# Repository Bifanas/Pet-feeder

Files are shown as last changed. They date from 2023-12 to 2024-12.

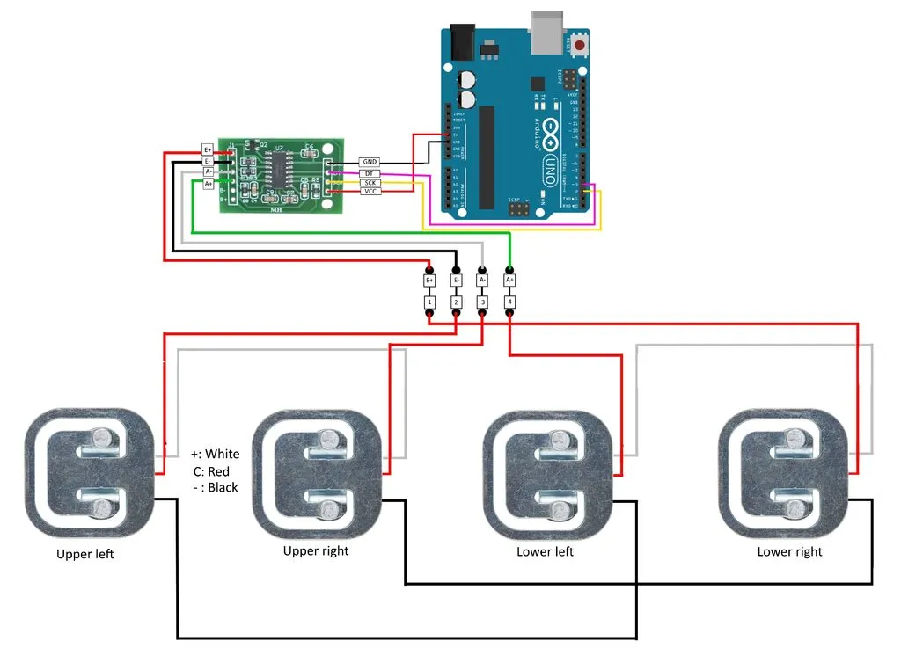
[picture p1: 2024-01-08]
Components testing/4-load-cells.png

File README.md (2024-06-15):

# Pet feeder 🐕

We designed an affordable dog feeder suitable for every kibble size and we hope that by sharing it, we can help more dog owners out there to create their perfect solution.



We are a small group of friends, designers, engineers, and dog owners. We needed to ensure our fluffy friends were always fed on time, even when we got stuck at school or work. And as we have large dogs any commercial solutions were unsuitable for our needs. That's how we started developing this dog feeder, first as a student project, and now as a passion. 

Our automated feeder is meant to help keep a consistent feeding schedule and ensure portion control. The design consists of 3d printed parts, a dispensing mechanism controlled by a motor, and a load cell to control the portion size. To run the dog feeder, it is important to set up a feeding schedule and also to manually calibrate the amount of food, that is being dispensed.

## Table of Contents
- [Features](#features)
- [List of Materials](#list)
- [Tutorials](#tutorials)
- [Contributing](#contributing)
- [Acknowledgments](#acknowledgments)

<br>

## Features
With this version of the automated feeder, you know exactly how many grams of food your dog was fed. 
Features include:
- manual calibration
- implemented load cell
- real time clock
- feeding schedule
- portion control and history log

<br>

## Contributing
1. Fork the repository
2. Create a new branch: `git checkout -b feature-name`
3. Make your changes and commit: `git commit -m "Add feature"`
4. Push to the branch: `git push origin feature-name`
5. Submit a pull request

<br>
## Acknowledgments
- Thanks to [Author Name](https://github.com/author) for the inspiration



The first version is available to solve the task of feeding your pet remotely.



Unique mechanism that is compatible with any size of dog kibble. 



It is possible to expand the storage size, for larger breads.

Assembly_2024-Jun-15_04-08-04PM-000_CustomizedView39398573342_png

Friendly and easy to maintain.

Assembly_2024-Jun-15_04-07-05PM-000_CustomizedView9829416363_png

Keep the previous meals' data to make sure your pet was fed the correct amount.

For the smallest to the biggest.

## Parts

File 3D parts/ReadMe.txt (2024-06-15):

This models were desingned to be able to fit into the most bascic printers.
No support is needed for any part. Recomend printing in PETG with a lower layer hight (<= 0.16mm).

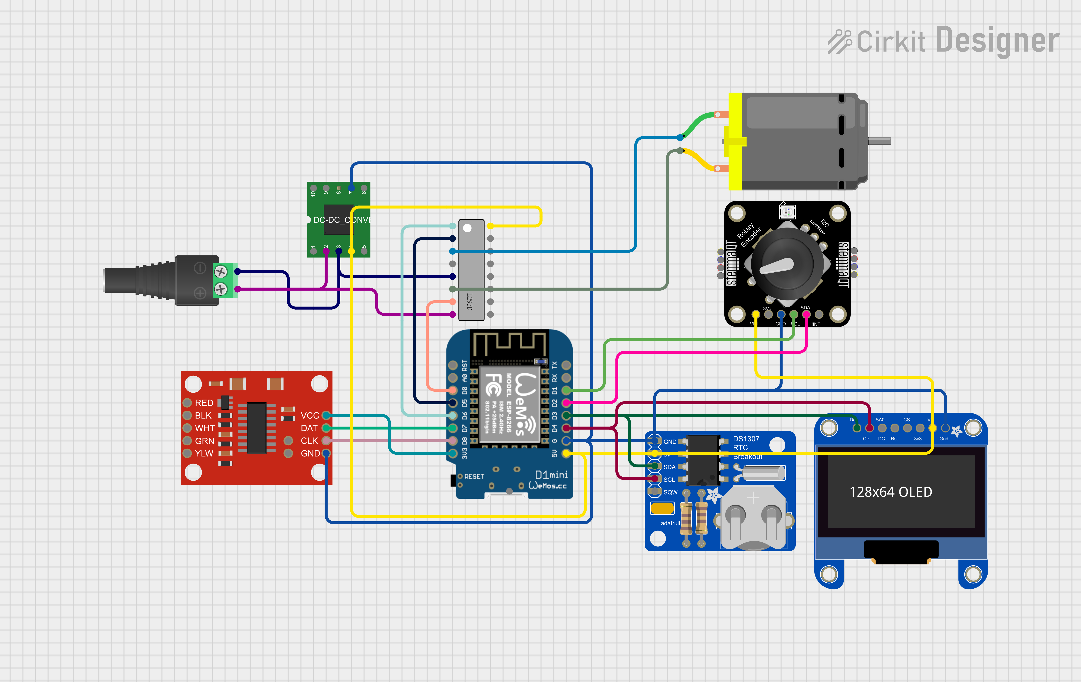
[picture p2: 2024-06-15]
Materials/circuit.png

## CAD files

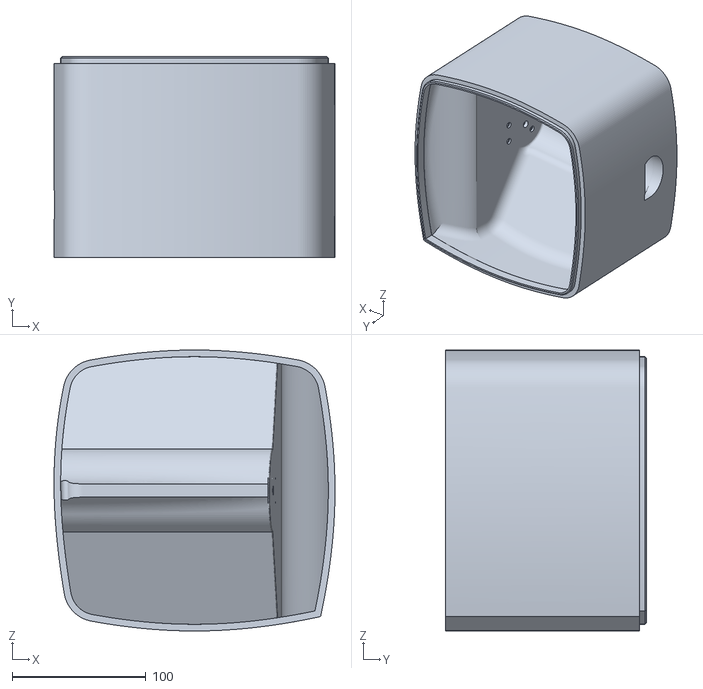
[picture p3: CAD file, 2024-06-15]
3D parts/Main.stl
210.0 x 150.0 x 210.0

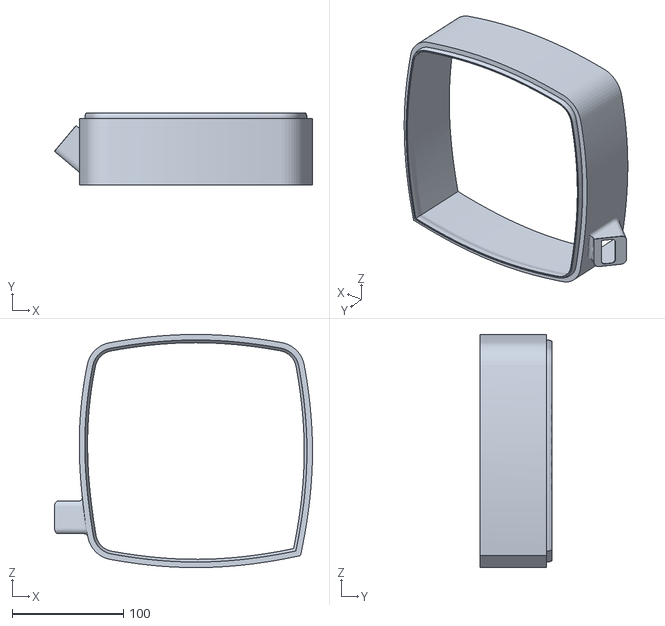
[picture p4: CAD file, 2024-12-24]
3D parts/Display adaptor.stl
232.3 x 65.0 x 210.0

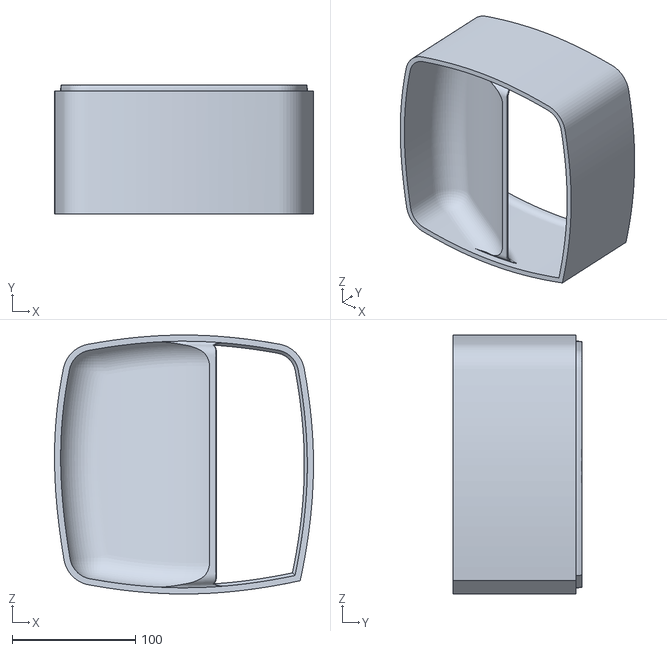
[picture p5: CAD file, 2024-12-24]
3D parts/Resivoir adaptor.stl
210.0 x 105.0 x 210.0

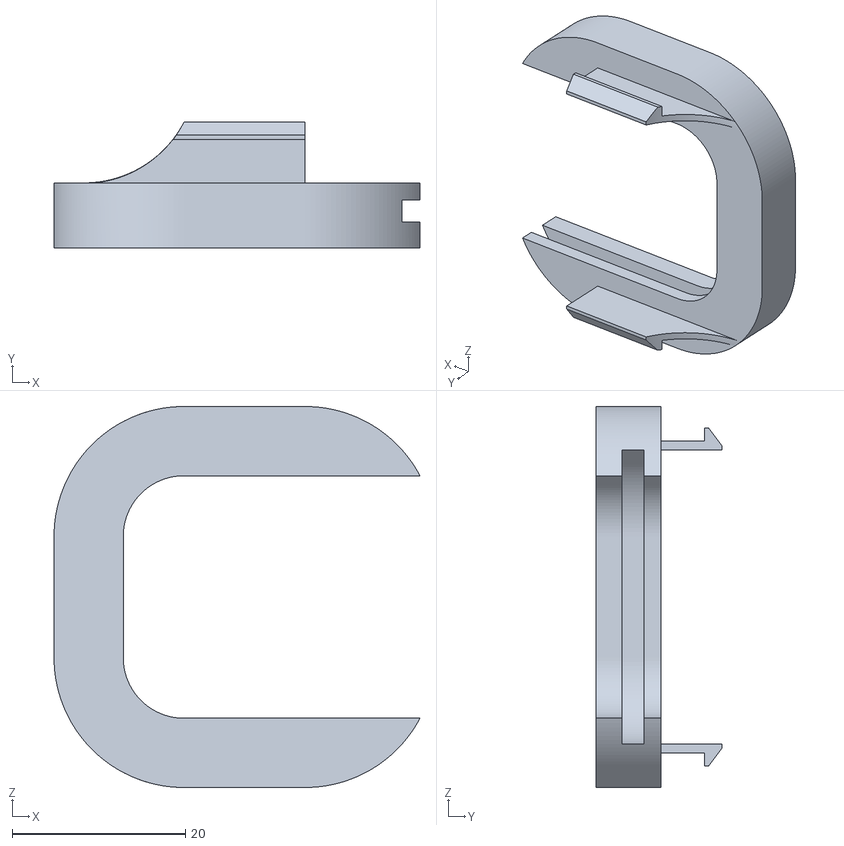
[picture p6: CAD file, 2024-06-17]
3D parts/Load cell.stl
42.3 x 14.5 x 44.0

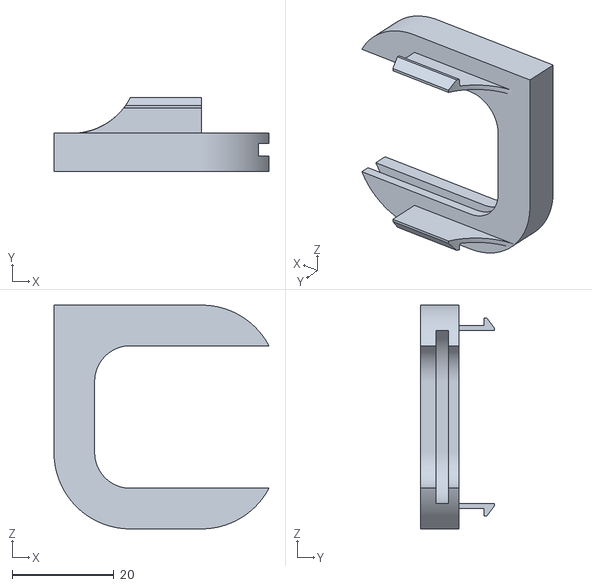
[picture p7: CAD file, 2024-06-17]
3D parts/Load cell corner.stl
42.3 x 14.5 x 44.0

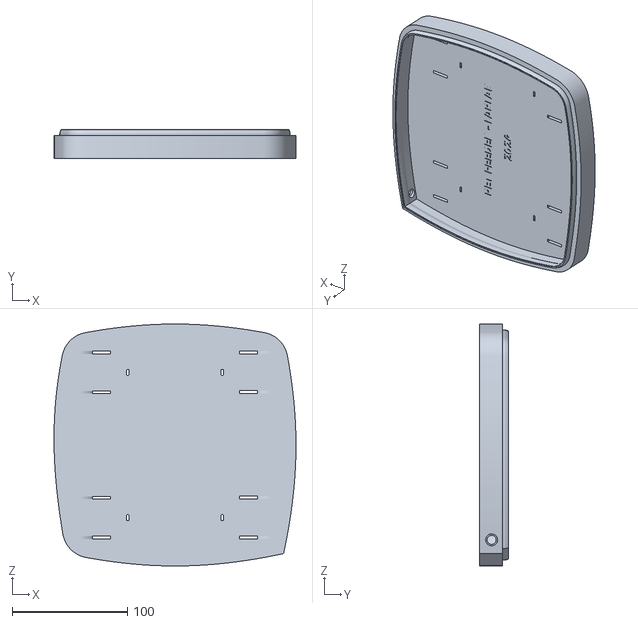
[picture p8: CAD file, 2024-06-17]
3D parts/Base.stl
210.0 x 25.0 x 210.0

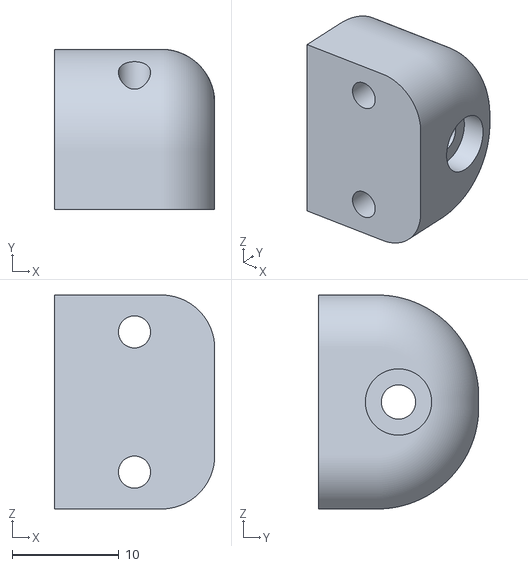
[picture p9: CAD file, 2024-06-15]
3D parts/motor atachment.stl
15.0 x 15.0 x 20.0

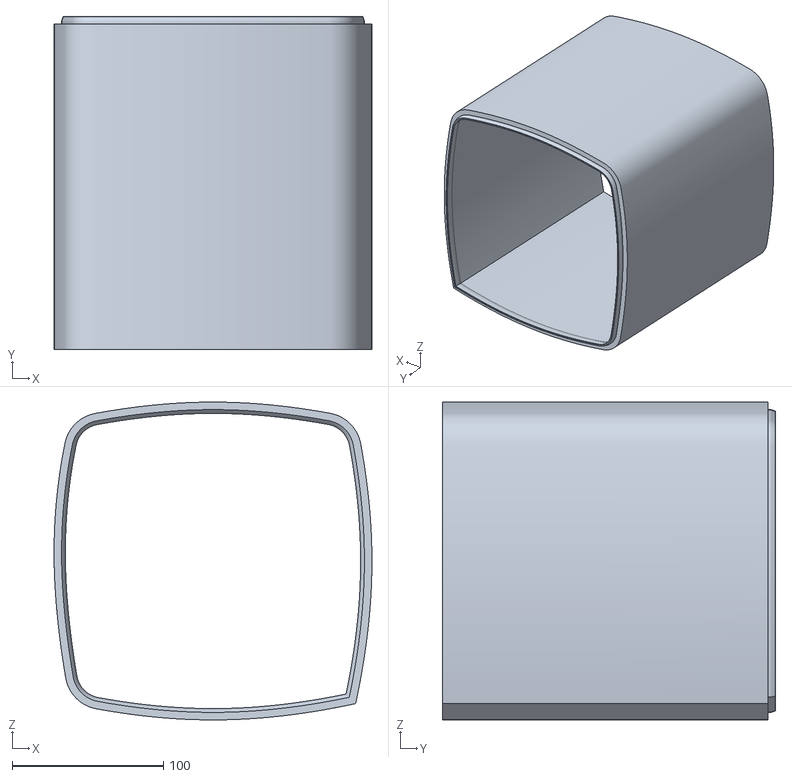
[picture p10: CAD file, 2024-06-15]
3D parts/Extension.stl
210.0 x 220.0 x 210.0

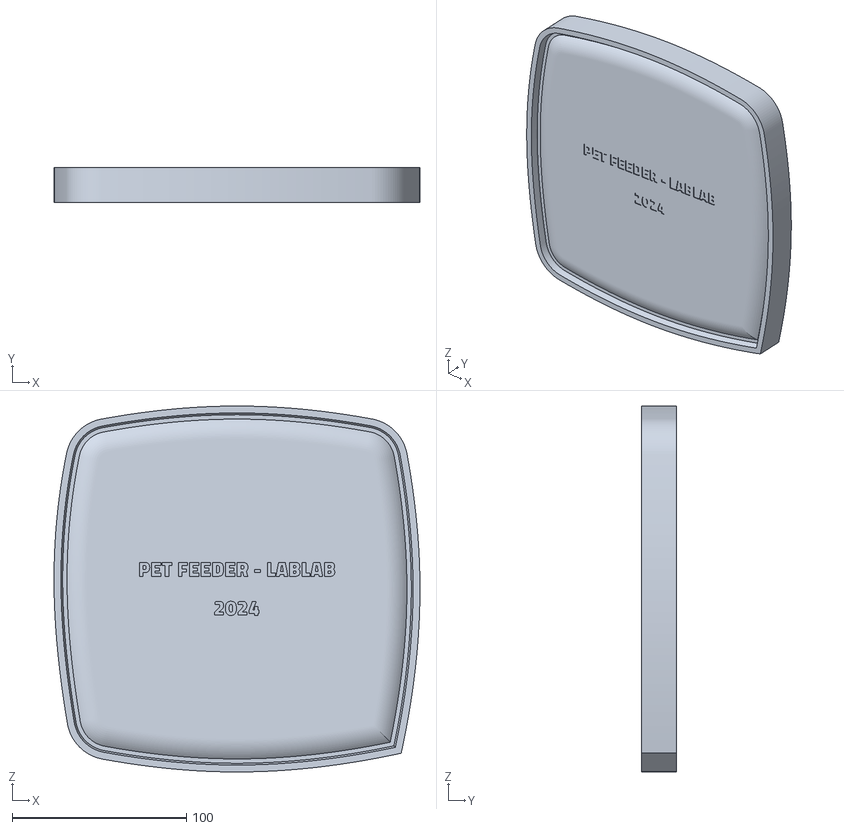
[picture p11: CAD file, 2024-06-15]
3D parts/Lid.stl
210.0 x 20.0 x 210.0

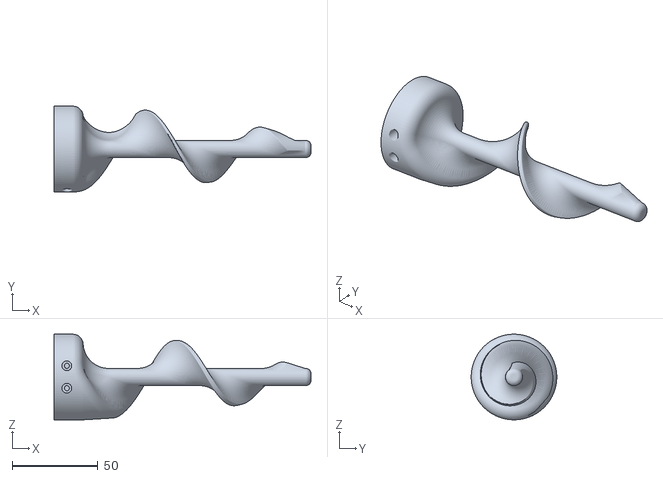
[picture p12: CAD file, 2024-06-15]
3D parts/Screw.stl
150.0 x 50.0 x 50.0

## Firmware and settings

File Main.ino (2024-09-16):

//////////////////////////////////////////////////////////////////
//                          LIBRARIES                           //
//////////////////////////////////////////////////////////////////

//LOAD CELL LIB-------------------------------------------------------------------------------------
#include "HX711.h"
HX711 scale;

//OLED DISP LIB-------------------------------------------------------------------------------------

#include <SPI.h>
#include <Wire.h>
#include <Adafruit_GFX.h>
#include <Adafruit_SSD1306.h>

// Real Time Clock LIB---------------------------------------------------------------------

#include "Arduino.h"
#include "uRTCLib.h"
uRTCLib rtc(0x68);  // uRTCLib rtc;

//////////////////////////////////////////////////////////////////
//                           DEFINES                            //
//////////////////////////////////////////////////////////////////

// LOAD CELL DEFINES--------------------------------------------------------------------------------

#define LOADCELL_DOUT_PIN 13
#define LOADCELL_SCK_PIN 15
float calibration_factor = 23.5; //need to czech

int weigth = 0;

// OLED DISP DEFINES--------------------------------------------------------------------------------

#define SCREEN_WIDTH 128  // OLED display width, in pixels
#define SCREEN_HEIGHT 64  // OLED display height, in pixels

// Declaration for SSD1306 display connected using I2C
#define OLED_RESET -1  // Reset pin
#define SCREEN_ADDRESS 0x3C
Adafruit_SSD1306 display(SCREEN_WIDTH, SCREEN_HEIGHT, &Wire, OLED_RESET);


const int bufferSize = 4;  // Size of the circular buffer
struct Measurement {
  char Calendar[20];
  float weight;
};

Measurement measurements[bufferSize];  // Array to store the measurements
int currentIndex = 0;                  // Index to keep track of the current position in the buffer

// RTC DEFINES--------------------------------------------------------------------------------

//char Calendar[20];  // string UTF8 end zero

// Motor DEFINES -----------------------------------------------------------------------------


 // Motor A connections
#define enA 17
#define in1 16
#define in2 14

float cal = 17.7;  // auxiliary declaration of an initial Calibration value
// calibration for 12V 28rpm float cal = 17.7;

int16_t Hour_A;  // 32767.. +32767  optimize the data type
int16_t Hour_B;

int16_t Minute_A;
int16_t Minute_B;

int16_t Meal_size_A;
int16_t Meal_size_B;


//////////////////////////////////////////////////////////////////
//                          FUNCTIONS                           //
//////////////////////////////////////////////////////////////////

void MotorControl(float time, bool direrction) {
  analogWrite(enA, 255); // Set motors to maximum speed

  if (direrction) {
    digitalWrite(in1, HIGH);  // 1 Forward
    digitalWrite(in2, LOW);
  } else if (!direrction) {  // 0 Reverse
    digitalWrite(in1, LOW);
    digitalWrite(in2, HIGH);
  }
  delay(time); // Keep spinning (Food control) 
  
  digitalWrite(in1, LOW); // Turn off motors
  digitalWrite(in2, LOW);

  analogWrite(enA, 0); // Disable the motors
}

//--------------------------------------------------------------------------------------


void feed(float cal, int amount) {
   float turns = 2900 * (50/ cal); //  (2900) = 1 tunr, 50g = portion size, cal = 18g per turn
  for (int i = 0; i < amount; i = i + 50) { // feeds in 50g pulses
  MotorControl(turns, 1); // Spins forward
  MotorControl(1000, 0);  // Spins backwards
  }
}


char now[20];

void addMeasurement(float newWeight, char current_calendar[]) {
  // Create a new measurement
  Measurement newMeasurement;
  strcpy(newMeasurement.Calendar, current_calendar);  // Use strcpy to copy the content
  newMeasurement.weight = newWeight;

  // Add the new measurement to the buffer at the current index
  measurements[currentIndex] = newMeasurement;

  // Increment the current index and wrap around if necessary
  currentIndex = (currentIndex + 1) % bufferSize;
}

void Main_screan_print() {
  //Serial.println("Buffer:");
  // Print the contents of the buffer

  /*
  for (int i = 0; i < bufferSize; i++) {
    Serial.print("Timestamp: ");
    Serial.print(measurements[i].Calendar);
    Serial.print(" Weight: ");
    Serial.println(measurements[i].weight, 2);
  }
  Serial.println();
  */

  display.clearDisplay();
  display.setTextSize(2);
  display.setTextColor(WHITE);
  display.setCursor(0, 0);
  display.print(rtc.hour());
  display.print(":");
  display.print(rtc.minute());
  display.print(":");
  display.print(rtc.second());
  display.setTextSize(1);
  display.print(" ");
  display.print(rtc.day());
  display.print("/");
  display.print(rtc.month());

  display.setCursor(0, 25);
  display.setTextSize(1);


  for (int i = 0; i < bufferSize; i++) {
   //display.print("");
    
    display.print(measurements[i].Calendar);
    display.print(" ");
    display.print(measurements[i].weight);
    display.println(" g");    
  }

  display.display();
}


void setup() {

  Serial.begin(9600);
  // MOTOR SETUP-----------------------------------------------------------------------------

  // Set all the motor control pins to outputs
  pinMode(enA, OUTPUT);
  pinMode(in1, OUTPUT);
  pinMode(in2, OUTPUT);

  // Turn off motors - Initial state
  digitalWrite(in1, LOW);
  digitalWrite(in2, LOW);

  // RTC SETUP-------------------------------------------------------------------------

  URTCLIB_WIRE.begin();

  //rtc.set(0,50,21, 6, 31, 8, 2024);  //(second, minute, hour, dayOfWeek, dayOfMonth, month, year)

  //LOAD CELL SETUP-------------------------------------------------------------------------------------

  scale.begin(LOADCELL_DOUT_PIN, LOADCELL_SCK_PIN);
  scale.set_scale(calibration_factor);      //Adjust to this calibration factor
  scale.tare();                             //Reset the scale to 0
  long zero_factor = scale.read_average();  //Get a baseline reading
  Serial.print("Zero factor: ");            //This can be used to remove the need to tare the scale. Useful in permanent scale projects.
  Serial.println(zero_factor);


  //OLED DISP SETUP-------------------------------------------------------------------------------------
  // initialize the OLED object
  if (!display.begin(SSD1306_SWITCHCAPVCC, SCREEN_ADDRESS)) {
    Serial.println(F("SSD1306 allocation failed"));
    for (;;)
      ;  // Don't proceed, loop forever
  }
  // Clear the buffer.
  display.clearDisplay();


  //////////////////////////////////////////////////////////////////
  //                    MEAL SCHEDULE SETUP                       //
  //////////////////////////////////////////////////////////////////

  // Change the time and size of the first meal!

  Hour_A = 8;
  Minute_A = 0;
  Meal_size_A = 200;

  // Change the time and size of the first meal!

  Hour_B = 17;
  Minute_B = 0;
  Meal_size_B = 200;
}

//////////////////////////////////////////////////////////////////
//                             MAIN                             //
//////////////////////////////////////////////////////////////////

int old_weigth = 0;
int new_weigth = 0;

unsigned long seconds = 1000L;  
unsigned long minutes = seconds * 60;



void loop() {
    //Updates the data ---------------------------------------------------------------------------------------

  rtc.refresh();  // Check the current time.

  sprintf(now, "%02d/%02d %02d:%02d", rtc.day(), rtc.month(), rtc.hour(), rtc.minute());
  Serial.println(now);

  Main_screan_print();

 // Serial.println(scale.get_units(5));  // Mesures how much food is inside.

  //schedule detection -------------------------------------------------------------------------------------
  if (Hour_A == rtc.hour() && Minute_A == rtc.minute() && 0 == rtc.second()) {

    old_weigth = scale.get_units(5);

    feed(cal, Meal_size_A);
    delay(5*minutes);

    new_weigth = scale.get_units(5);
    old_weigth = old_weigth - new_weigth;

    addMeasurement(old_weigth, now);
  }
  if (Hour_B == rtc.hour() && Minute_B == rtc.minute() && 0 == rtc.second()) {
    
    old_weigth = scale.get_units(5);
    
    feed(cal, Meal_size_B);
    delay(5*minutes);

    new_weigth = scale.get_units(5);
    old_weigth = old_weigth - new_weigth;
    addMeasurement(old_weigth, now);
  }
  delay(500);
}

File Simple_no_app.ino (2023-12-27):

//////////////////////////////////////////////////////////////////
//                          LIBRARIES                           //
//////////////////////////////////////////////////////////////////


//LOAD CELL LIB-------------------------------------------------------------------------------------
#include "HX711.h"
HX711 scale;

//OLED DISP LIB-------------------------------------------------------------------------------------

#include <SPI.h>
#include <Wire.h>
#include <Adafruit_GFX.h>
#include <Adafruit_SSD1306.h>

// Real Time Clock LIB---------------------------------------------------------------------

#include "Arduino.h"
#include "uRTCLib.h"
uRTCLib rtc(0x68);  // uRTCLib rtc;


//////////////////////////////////////////////////////////////////
//                           DEFINES                            //
//////////////////////////////////////////////////////////////////

// LOAD CELL DEFINES--------------------------------------------------------------------------------


#define LOADCELL_DOUT_PIN 18
#define LOADCELL_SCK_PIN 19
#define calibration_factor 106

int weigth = 0;


// OLED DISP DEFINES--------------------------------------------------------------------------------

#define SCREEN_WIDTH 128  // OLED display width, in pixels
#define SCREEN_HEIGHT 64  // OLED display height, in pixels

// Declaration for SSD1306 display connected using I2C
#define OLED_RESET -1  // Reset pin
#define SCREEN_ADDRESS 0x3C
Adafruit_SSD1306 display(SCREEN_WIDTH, SCREEN_HEIGHT, &Wire, OLED_RESET);

// RTC DEFINES--------------------------------------------------------------------------------

char Calendar[20];  // string UTF8 end zero

// Motor DEFINES -----------------------------------------------------------------------------

const int enable_motor = 15;
const int step = 2;
const int dirPin = 4;

float cal = 49;  // auxiliary declaration

int16_t Hour_A;  // 32767.. +32767
int16_t Hour_B;  // 32767.. +32767

int16_t Minute_A;  // 32767.. +32767
int16_t Minute_B;  // 32767.. +32767


int16_t Meal_size_A;  // 32767.. +32767
int16_t Meal_size_B;  // 32767.. +32767



//////////////////////////////////////////////////////////////////
//                          FUNCTIONS                           //
//////////////////////////////////////////////////////////////////


void stepper(float Screw_turns, int motorpin, bool direction) {

  int speed = 600;  //NEEDS TO BE CALIBRATED !!!
  int full_turn = 4000;

  int steps = Screw_turns * full_turn;  // get how many steps

  digitalWrite(enable_motor, LOW);
  digitalWrite(dirPin, direction);

  for (int x = 0; x < steps; x++) {
    digitalWrite(motorpin, HIGH);
    delayMicroseconds(speed);
    digitalWrite(motorpin, LOW);
    delayMicroseconds(speed);
  }
  digitalWrite(enable_motor, HIGH);
}


//--------------------------------------------------------------------------------------

void feed(float cal, int amount) {
  //  to get how many turns to get 50g
  float turns = 50 / cal;
  for (int i = 0; i <= amount; i = i + 50) {
    stepper(turns, step, HIGH);  //1 turn = 4000 steps = 103g
    stepper(0.2, step, LOW);     //spins backwards chug control
  }
  digitalWrite(enable_motor, HIGH);
}





//////////////////////////////////////////////////////////////////
//                            SETUP                            //
//////////////////////////////////////////////////////////////////

void setup() {
  Serial.begin(9600);
  // MOTOR SETUP-----------------------------------------------------------------------------

  pinMode(enable_motor, OUTPUT);
  pinMode(step, OUTPUT);
  pinMode(dirPin, OUTPUT);

  // RTC SETUP-------------------------------------------------------------------------

  URTCLIB_WIRE.begin();
  // rtc.set(0, 52, 22, 4, 22, 11, 2023);  // rtc.set(second, minute, hour, dayOfWeek, dayOfMonth, month, year)

  //LOAD CELL SETUP-------------------------------------------------------------------------------------

  scale.begin(LOADCELL_DOUT_PIN, LOADCELL_SCK_PIN);
  scale.set_scale(calibration_factor);      //Adjust to this calibration factor
  scale.tare();                             //Reset the scale to 0
  long zero_factor = scale.read_average();  //Get a baseline reading
  Serial.print("Zero factor: ");            //This can be used to remove the need to tare the scale. Useful in permanent scale projects.
  Serial.println(zero_factor);
  scale.tare();  //Reset the scale to 0

  //OLED DISP SETUP-------------------------------------------------------------------------------------
  // initialize the OLED object
  if (!display.begin(SSD1306_SWITCHCAPVCC, SCREEN_ADDRESS)) {
    Serial.println(F("SSD1306 allocation failed"));
    for (;;)
      ;  // Don't proceed, loop forever
  }
  // Clear the buffer.
  display.clearDisplay();

  //MEAL SCHEDULE SETUP-------------------------------------------------------------------------------------
  Hour_A = 7;
  Minute_A = 0;
  Meal_size_A = 200;


  Hour_B = 16;
  Minute_B = 0;
  Meal_size_B = 200;
}


//////////////////////////////////////////////////////////////////
//                             MAIN                             //
//////////////////////////////////////////////////////////////////

int old_weigth = 0;
int new_weigth = 0;
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

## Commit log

2023-12-27 Current version. v.1.8
    Simple code. Implementation of the motor, scale, clock, and screen. Only 2 meals a day. And schedule and portion has to be defined on the code. No implementation of loadcell or motor calibrations.
2024-01-01 STL files for the version V1.1
    [Base.stl, Body.stl, Guide.stl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]
2024-01-01 Create Material list
    Links for shopping the materials
2024-01-02 Create Circuit
2024-01-02 Current circuit
2024-01-02 Update and rename Circuit to Material List
2024-06-08 Create Material List for V9
2024-06-08 Rename 3D Parts/dogfeeder v9.3mf to 3D Parts/V9/dogfeeder v9.3mf
    [dogfeeder v9.3mf]
2024-06-15 Rename Material List for V9 to Material List
2024-12-24 new updates
    display adaptor, supposed to be placed under the Main and over the loadcells, have space to add a 128x64 OLED display
    The Resivoir adaptor helps reduce the general weight of the food on top of the screw assembly, further more support for a Uv sterilization light
    [Display adaptor.stl, Resivoir adaptor.stl]
